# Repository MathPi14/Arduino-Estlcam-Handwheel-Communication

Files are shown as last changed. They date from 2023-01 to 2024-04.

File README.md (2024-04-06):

# [GERMAN VERSION](https://github.com/MathPi14/Arduino-Estlcam-Handwheel-Communication/blob/main/README_DE.md)

# Table of contents
* [General Description](#general-description)
* [Prerequisites](#prerequisites)
* [Installation](#installation)
* [Used Components](#used-components)

## General Description
This is my implementation of the Estlcam handwheel i2c communication protocol (https://www.estlcam.de/DIN_Detail.php) for Arduino Boards. 
Its made for users of the original Estlcam Hardware.

The Code supports all the features the originial handwheel provides:
* 3/4 - axis joystick for rough positioning 
* encoder (handwheel) which allows very fine positioning
* spindle, program start and enter (probing) buttons 
* feed and speed override potentiometers

the following 'hidden' features are implemented as well:
* 3 led which indicate which of the axis is currently active to move on the handwheel
* 3 buttons to change the currently active axis 
* emergency stop (triggers program pause)

top
inside
inside_2
Unbenannt

Tested with Estlcam V11.244. The hidden features may not be supported by other Estlcam Versions.
	
## Prerequisites
To get started, you need the following:
* an original Estlcam board with a mini-DIN port
* mini-DIN cable (6 Pin, male connector). 2-3 m length recommended, depending on the size of your cnc. Super long cables (>5 m) might cause EMC issues
* an arduino (original or compatible) board with 5 V operating voltage, 7 ADC Pins including SDA and SCL for the i2c communication functionality and 9 digital Pins like the Arduino Nano 
* analog joystick (3 or 4 axis, 10kohm)
* handwheel encoder
* 2x 10kohm potentiometers
* 6x push buttons. No toggle switches!
* 3x 5 V LED (or 12 V with appropiate resistor)
* emergency stop button
* housing (see attached .stl files)
* a small cable gland (M16/ PG9 if you use my 3d printed housing)
* 4 M4 brass inserts and short screws (if you use my 3d printed housing)

You also need basic soldering equipment, cables, shrink tubing, hot glue etc.
	
## Installation
### Housing/ Electronics
* start with installing the led, push-buttons, the encoder and potentiometers (not the joystick, arduino, cable gland and emergency stop for now). Carefully solder (not too short) cables to the components. It's recommended to use the screw terminals of the handwheel encoder as bus for the components and the DIN Cable as well. This way, the DIN cable remains detatchable
* secure the cables with hot glue
* solder the cables to the arduino according the attached photo of the pinout. Use two short cables for the SDA and SCL so that we can connect them to the DIN cable with Wago clamps later (the cable remains detachable, see #1)
* attach the arduino to the insert and sort the cables with the cable comb
* insert the DIN cable, connect enc + and - as well as VCC and GND to the encoder (handwheel) and SDA/ SCL to the arduino

### Software (Arduino)
Flash the Arduino via the IDE. The onboard TX LED blinks when the program is running. 
If you use any other arduino board or if your pin assignment differs from mine, you may need to change the following defines 

```
#define JOYSTICK_X_GPIO A0            
#define JOYSTICK_Y_GPIO A1
#define JOYSTICK_Z_GPIO A2
#define SPEED_GPIO A6                  
#define SPEED_GPIO_INVERTED 1          
#define FEED_GPIO A7                   
#define FEED_GPIO_INVERTED 1            

#define X_LED_GPIO 2
#define Y_LED_GPIO 3
#define Z_LED_GPIO 4

#define X_SELECT_GPIO 5
#define Y_SELECT_GPIO 6
#define Z_SELECT_GPIO 7          
#define SPINDLE_START_GPIO 8    
#define PROGRAM_START_GPIO 9
#define OK_GPIO 10                   
#define STOP_GPIO 11         

#define ONBOARD_LED_GPIO 13           
```

### Software (Estlcam)
After the electrical work is done and the Code is running on your Arduino, you can connect the mini-DIN cable to the Estlcam Board and reprogram the latter. You know that everything worked out, if there's a 'Handrad 0001 ...' line appearing in the log inside Estlcam. If it didn't, there is most likely something wrong with the SDA/ SCL Pins.

If it works, you can go to the controls tab inside Estlcam and test the components. If the Joystick ADC are inverted, you can simply change it in Estlcam directly. If the Buttons, LED or feed/ speed potentiometers are inverted or not assigned correctly, go back to the previous step and change the defines

## Used Components
* joystick (https://de.aliexpress.com/item/4001270851701.html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)
* encoder (5V 4Pin, 60 mm) (https://de.aliexpress.com/item/32949618549.html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)
* buttons (https://de.aliexpress.com/item/1005003302861259.html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)
* 5V led (https://de.aliexpress.com/item/1005003751324053.html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) 
* 10 kOhm potentiometers (https://de.aliexpress.com/item/4000971762879.html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)
* emergency stop (16 mm diameter) (https://de.aliexpress.com/item/33014058927.html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)
* Arduino Nano (https://de.aliexpress.com/item/1005002867053794.html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)

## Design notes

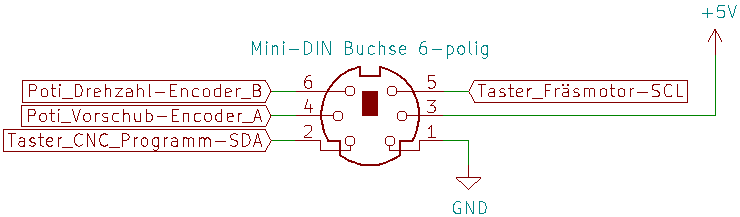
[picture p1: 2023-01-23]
DIN_cable.png

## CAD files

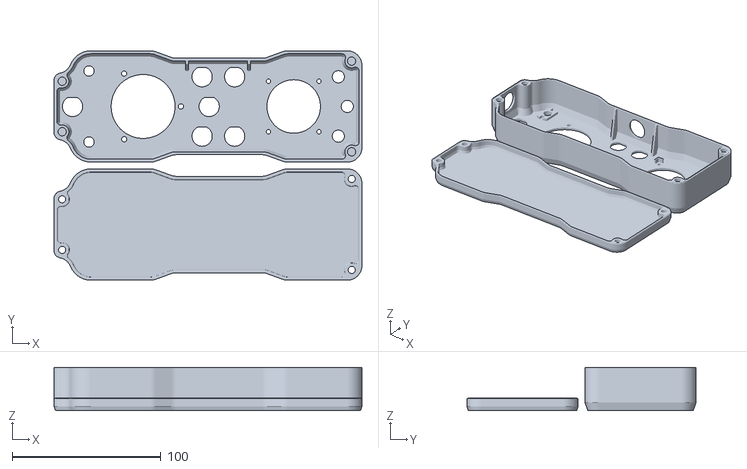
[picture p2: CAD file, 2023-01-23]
housing.stl
207.4 x 154.5 x 29.0

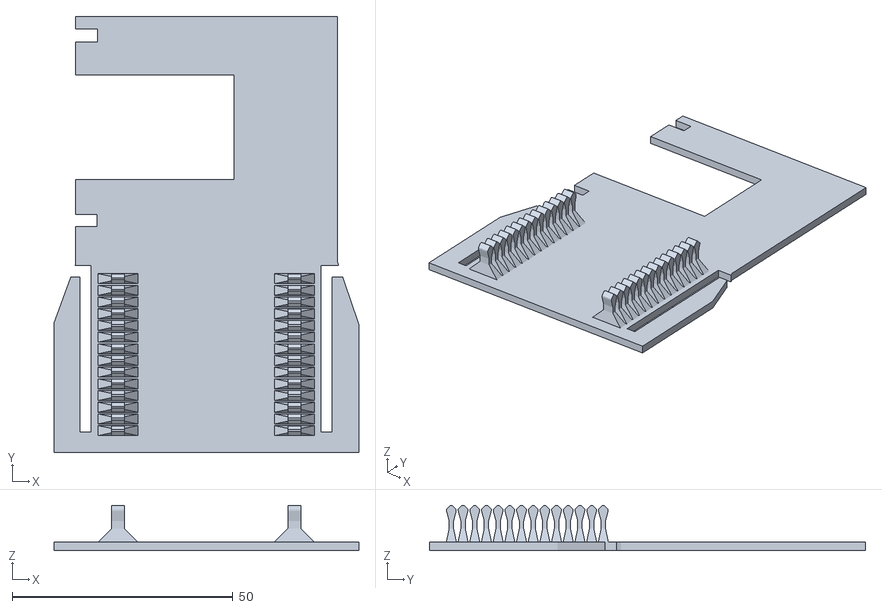
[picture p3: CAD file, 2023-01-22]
insert.stl
69.1 x 98.9 x 10.3

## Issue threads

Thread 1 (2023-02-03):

Use HWInterrupts instead of polling to register changing states of all buttons

MathPi14, 2023-02-03:
Not all Arduinos come with 5 Interrupt Pins. In oder to make the code less dependent from the used hardware, polling is used to register button change "events". This can lead to a sluggish response.

In a future release, PinChangeInterrupts (see Arduino site) shall be used to solve this problem. These dont work like "normal" Interrupts and always trigger on both the rising and falling edge. Debouncing and faster Read/ Write cycles (e.g. with direct port manipulation) are necessary.

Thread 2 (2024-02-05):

old vs new version - potentiometers do not work

KaHu85, 2024-02-05:
Hello MathPi14,

we are having a [discussion here](https://www.cnc-aus-holz.at/index.php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) about the old and new code.
Somehow the new code does not work with the pots.
Found the old code from 21.7.2022,
now the potentiometers work.

Can you have a look over it?
It's just the calculation for the potentiometers that's different, isn't it?

Would be great if you could take a look at it and shed some light on why it doesn't work with the new code.
Regards Alex

KaHu85, 2024-02-06:
Hallo Matthias, ah okay...
Ja ich habe es dann nur mal verglichen alt mit neu und die Zahlen die raus kommen sind aber annähernd gleich. Deshalb habe ich es nicht verstanden wieso es mit der alten Version scheinbar funktioniert. Jedenfalls konnte ich ihnen etwas helfen, Sie haben es jetzt zum laufen gebracht, jedoch witzigerweise nur bis zu einer gewissen Estlcam Version. Keine Ahnung was da in Estlcam geändert wurde wieso es dann aufeinmal nicht mehr geht. Danke und bis bald. LG Alex

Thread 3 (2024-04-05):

Schaltplan

Tino51078, 2024-04-05:
Hallo Matthias,

ich bin durch Zufall auf dein Projekt gestoßen und würde das gerne nachbauen. Leider fehlt mir ein wenig (viel) Erfahrung mit den Arduino´s. Ich habe mal versucht deinen Aufbau in einem Schaltplan zusammenzufassen. Leider kann ich nicht allen in deinem Gehäuse erkennen. Somit kann natürlich erstmal nicht alles in dem Plan stimmen. Es wäre sehr freundlich von dir, wenn du dir bei Gelegenheit die Zeit nehmen könntest um die Fehlenden Sachen zu korrigieren. Wenn du willst, kann ich dann den fertigen, geänderten Plan zu deiner Bauanleitung bereitstellen. Würde mich über deine Unterstützung sehr freuen.

Viele Grüße
Tino
[Schaltplan.pdf](https://github.com/MathPi14/Arduino-Estlcam-Handwheel-Communication/files/14890862/Schaltplan.pdf)

MathPi14, 2024-04-06:
Hallo Tino, ich habe meinen Schaltplan erweitert. Habe zwar leider kein so tolles CAD Programm wie du, aber das sollte dir weiterhelfen. Es kann natürlich vorkommen, dass die Farbcodierung der Chinesen mal abweicht (Joystick), also würde vorschlagen, dass du die Belegung vorher testest z. B. mit Multimeter. Alternative: Trial and Error am Arduino.
Gruß Matthias

Tino51078, 2024-04-06:
Hallo Matthias,
jetzt bin ich ein wenig verwirrt. an die 5 Potis müssen bestimmt je 3 Kabel. (+/-und die Funktion)Bedeutet bestimmt die roten Leitungen aus deinem Schaltplan liegen am Mittelanschluss und die jetzigen roten am Poti wären 5v. Vermute ich mal. Aber mehr verwirrt mich der encoder. In deinem Aufbau ist definitiv 0V und Vcc belegt nicht A&B. Tut mir leid, ich will dir nicht auf die Nerven gehen. Möchte nur keine Fehler einbauen und defekte provozieren.....  Nochmal kurz zu meiner Frage bei "CNC aus Holz"
Mit dem Arduino UNO wird dein Aufbau so nicht gehen, Oder? Weil der weniger PIN´s als der NANO hat...?

Grüße Tino

MathPi14, 2024-04-06:
> an die 5 Potis müssen bestimmt je 3 Kabel. (+/-und die Funktion)Bedeutet bestimmt die roten Leitungen aus deinem Schaltplan liegen am Mittelanschluss und die jetzigen roten am Poti wären 5v
Der Mittlere Anschluss an den Potis ist immer das Signal, die anderen beiden GND und VCC (kann man auch vertauschen, dann ist das Signal physisch invertiert - Achse fährt verkehrt herum -, kann aber logisch in Estlcam wieder "umgedreht" werden. Bei den Geschwindigkeits-Potis muss man im Code ein Flag setzen (da bietet Estlcam keine Möglichkeit)

> Aber mehr verwirrt mich der encoder. In deinem Aufbau ist definitiv 0V und Vcc belegt nicht A&B
GND und VCC müssen schon auch belegt werden, sonst funktioniert der Encoder nicht. Die beiden **nicht belegten** anschlüsse sind dann Encoder A und B. Der Anschluss der Mini-Din-Buchse (dort sind die Kabel für Enc A/B) ist nicht auf den Bildern drauf, da man sonst nichts mehr erkennen würde :)

> Mit dem Arduino UNO wird dein Aufbau so nicht gehen, Oder?
Richtig

Du nervst nicht, mein Plan ist natürlich eine Bastlerlösung und deswegen sehr grob. Daher ja auch der Hinweis, dass man idealerweise etwas Erfahrung und (bei solchen DIY Projekten sowieso) Frusttoleranz mitbringen sollte.

hope that helps
Matthias

Tino51078, 2024-04-06:
Matthias,

vielen vielen ank für die Unterstützung. Ja ich habe schon in einigen Sachen Erfahrung. Ich lerne aber auch gerne dazu. Dabei möchte ich gerne soviel Fehlerquellen wie möglich vorab ausschließen. Deshalb auch meine vielen Nachfragen. Ich würde sehr gerne den Plan mit allen Komponenten nochmal zeichnen. Vielleicht kannst du dann nochmal drüber schauen? Ich konnte ja deinen Neid über mein CAD durchs WLAN spüren... Nein, ist nur Spaß... Aber falls der Plan dann okay ist, kann er auch gerne in deine Doku, falls du das möchtest. Ich werde jetzt auch nach deinem Vorbild zeichnen, der ist deutlich übersichtlicher.

Tino51078, 2024-04-06:
> Du nervst nicht, mein Plan ist natürlich eine Bastlerlösung und deshalb sehr grob. Daher ja auch der Hinweis, dass man idealerweise etwas Erfahrung und (bei solchen DIY-Projekten sowieso) Frusttoleranz mitbringen sollte.

Eine Bastlerlösung ist das bei weitem nichtmehr. Das ist schon ein nahezu perfektes Projekt. Die Gedanken dazu soll sich erstmal einer machen...

Tino51078, 2024-04-06:
Ich denke, so sollte es passen. Sind jetzt alle Komponenten drauf...
[Schaltplan Handrad.pdf](https://github.com/MathPi14/Arduino-Estlcam-Handwheel-Communication/files/14893951/Schaltplan.Handrad.pdf)

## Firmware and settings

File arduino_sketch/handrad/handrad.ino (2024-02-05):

/*
  Created on 21.07.2022 by MathPi 
  https://github.com/MathPi14/Arduino-Estlcam-Handwheel-Communication/edit/main/README.md#used-components      
*/

#include <Wire.h>

#define JOYSTICK_X_GPIO A0              // ADC Pins the Joystick, speed, feed ovveride potis are connected to
#define JOYSTICK_Y_GPIO A1
#define JOYSTICK_Z_GPIO A2
#define SPEED_GPIO A6                  
#define SPEED_GPIO_INVERTED 1          // 1 if the Poti values shall be inverted 
#define FEED_GPIO A7                   
#define FEED_GPIO_INVERTED 1            // see above

#define X_LED_GPIO 2
#define Y_LED_GPIO 3
#define Z_LED_GPIO 4

#define X_SELECT_GPIO 5                 // Digital IO the corresp. buttons are connected to
#define Y_SELECT_GPIO 6
#define Z_SELECT_GPIO 7
#define PROGRAM_START_GPIO 8           
#define SPINDLE_START_GPIO 9           
#define OK_GPIO 10                   
#define STOP_GPIO 11

#define ONBOARD_LED_GPIO 13             // "-" onboard led

#define DEBUG 0

#define I2C_ADRESS 0b0000010            // I2C Slave Adress
#define I2C_CLOCK_FREQUENCY 10000       // I2C Clock Frequency
#define IDENT_STRING "Handrad 0001"     // Response to Mode3: Identify
#define SERIALNO_STRING "ABCD12345678"  // Response to Mode5: Serial Number
#define READ_FRAME_SIZE 9               // Number of incoming Bytes on I2C Receive event
#define SEND_FRAME_SIZE 15              // "-" outgoing Bytes on I2C Request event

const uint8_t CHALLENGE_VAL[] = {0x3B, 0x59, 0xE8, 0x2A, 0xE9, 0xB1, 0xBE, 0xD8, 0x00, 0x00, 0x00, 0x00}; //Response to Mode5: Challenge
volatile uint8_t rcv_frame[9];          // 9 byte buffer for the received frames, needs to be volatile because it is changed on hardware interrupts
uint8_t send_frame[15];                 // 15 byte array for the values to send, must not be volatile because they are only updated in the loop()
volatile uint16_t speed_data;                    // 2 byte value for the analog speed ovveride (on SPEED_GPIO)
volatile uint16_t feed_data;                     // same as above
volatile uint16_t x_data;
volatile int16_t y_data;
volatile uint16_t z_data;
volatile uint8_t crc;                            // 1 byte value for the checksum (byte 15)
volatile bool program_start_btn_pressed;
volatile bool spindle_start_btn_pressed;
volatile bool ok_btn_pressed;
volatile bool stop_btn_pressed;
volatile uint8_t axis_selected;

// setup called once on program start
void setup() {
  Wire.begin(I2C_ADRESS);               // initialize device as peripheral with I2C_ADRESS (specified by Estlcam)
  Wire.setClock(I2C_CLOCK_FREQUENCY);   // set clock frequency to I2C_CLOCK_FREQUENCY (specified by Estlcam)
  Wire.onRequest(RequestEventHandler);  // register RequestEventHandler on Request Events from the Master (Estlcam)
  Wire.onReceive(ReceiveEventHandler);  // register ReceiveEventHandler on Receive Events from the Master (Estlcam)
  pinMode(PROGRAM_START_GPIO, INPUT_PULLUP);                    // initialize Button and Led GPIOs
  pinMode(SPINDLE_START_GPIO, INPUT_PULLUP);
  pinMode(OK_GPIO, INPUT_PULLUP);
  pinMode(STOP_GPIO, INPUT_PULLUP);
  pinMode(X_SELECT_GPIO, INPUT_PULLUP);
  pinMode(Y_SELECT_GPIO, INPUT_PULLUP);
  pinMode(Z_SELECT_GPIO, INPUT_PULLUP);
  pinMode(X_LED_GPIO, OUTPUT);
  pinMode(Y_LED_GPIO, OUTPUT);
  pinMode(Z_LED_GPIO, OUTPUT);
  pinMode(ONBOARD_LED_GPIO, OUTPUT);
#ifdef DEBUG
  Serial.begin(9600);
  Serial.println("Running");
#endif
}

// loop is called constantly
// handle mode state machine specified by Estlcam
void loop() {
  buffer_data();
  switch (rcv_frame[0]) 
  {
    case 0:
      delay(100);
      break;

    case 1:
      update_data();                                // update mode specific data
      break;

    case 2:
      update_data();                                // update mode specific data
      update_status_led();
      break;

    case 3:
      identify();
      break;

    case 4:
      challenge();
      break;

    case 5:
      serialnumber();
      break;
  }
}

//
void update_status_led() {
  switch (rcv_frame[1]) {
    case 0:
      digitalWrite(X_LED_GPIO, 0);
      digitalWrite(Y_LED_GPIO, 0);
      digitalWrite(Z_LED_GPIO, 0);
      break;

    case 1:
      digitalWrite(X_LED_GPIO, 1);
      digitalWrite(Y_LED_GPIO, 0);
      digitalWrite(Z_LED_GPIO, 0);
      break;

    case 2:
      digitalWrite(X_LED_GPIO, 0);
      digitalWrite(Y_LED_GPIO, 1);
      digitalWrite(Z_LED_GPIO, 0);
      break;

    case 4:
      digitalWrite(X_LED_GPIO, 0);
      digitalWrite(Y_LED_GPIO, 0);
      digitalWrite(Z_LED_GPIO, 1);
      break;
  }
}
// called on a i2c Request from the Master (Estlcam)
// interrupts the loop() thus needs to be as fast as possible
// increment Frame number and checksum according to Specification from Estlcam
void RequestEventHandler() {
  if (rcv_frame[0] != 0) {
    send_frame[12] = rcv_frame[0];                // set 12 bit to match selected mode
    send_frame[13] += 1;                          // increment frame on 13 byte
    send_frame[14] = crc_calc();                  // calculate checksum on 14 byte
    Wire.write(send_frame, sizeof(send_frame));   // Write new frame to the Master
  }
#ifdef DEBUG
  Serial.print("received : ");
  for (int i = 0; i < READ_FRAME_SIZE; i++) {
    if ((int)rcv_frame[i] < 20) {
      Serial.print("0");
    }
    Serial.print(rcv_frame[i], HEX);
    Serial.print(" ");
  }
  Serial.print("; sending: ");
  for (int i = 0; i < SEND_FRAME_SIZE; i++) {
    if ((int)send_frame[i] < 20) {
      Serial.print("0");
    }
    Serial.print(send_frame[i], HEX);
    Serial.print(" ");
  }
  Serial.println("");
#endif
}

// called on a i2c Request from the Master (Estlcam)
// interrupts the loop() thus needs to be as fast as possible and needs a volatile buffer to write data to
// save byte 1 of the received frame (specifies the  mode used in the loop() state machine)
void ReceiveEventHandler(int rcv_frame_size) {
  if (rcv_frame_size == READ_FRAME_SIZE) {        // check if we receive 9 bytes (according to specification from Estlcam)
    for (int i = 0; i < READ_FRAME_SIZE; i++) {   // save received data byte-by-byte to the volatile buffer variable
      rcv_frame[i] = Wire.read();
    }
  }
#ifdef DEBUG
  Serial.println("Receive Request");
#endif
}

void update_data() {
  send_frame[0] = 0xFF;                     //byte 1 = 255 according to spec
  if (axis_selected > 0) {
    send_frame[0] &= ~(1 << axis_selected - 1) | (0 << axis_selected - 1);
  }

  send_frame[1] = 0xFF;                     //set bits 2, 4,5,6,7 of byte 2 to 1 beforehand
  if (!program_start_btn_pressed) {
    send_frame[1] &= ~(1 << 0) | (0 << 0); //flip bit 0 if PROGRAM_START_GPIO is high
  }
  if (!spindle_start_btn_pressed) {
    send_frame[1] &= ~(1 << 1) | (0 << 1); //flip bit 1 if SPINDLE_START_GPIO is high
  }
  if (!ok_btn_pressed) {
    send_frame[1] &= ~(1 << 3) | (0 << 3); //flip bit 3 if OK_GPIO is high
  }
  if (stop_btn_pressed) {
    send_frame[1] &= ~(1 << 2) | (0 << 2); // stop
  }

  send_frame[2] = lowByte(speed_data);
  send_frame[3] = highByte(speed_data);
  send_frame[4] = lowByte(feed_data);
  send_frame[5] = highByte(feed_data);
  send_frame[6] = lowByte(x_data);
  send_frame[7] = highByte(x_data);
  send_frame[8] = lowByte(y_data);
  send_frame[9] = highByte(y_data);
  send_frame[10] = lowByte(z_data);
  send_frame[11] = highByte(z_data);
}

// called once after a Request Event fired and we are in mode 1
// update the data to write out to the master
void buffer_data() {
  program_start_btn_pressed = digitalRead(PROGRAM_START_GPIO);
  spindle_start_btn_pressed = digitalRead(SPINDLE_START_GPIO);
  ok_btn_pressed = digitalRead(OK_GPIO);
  stop_btn_pressed = digitalRead(STOP_GPIO);
  if (digitalRead(X_SELECT_GPIO) == 0) {
    axis_selected = 1;
  }
  else if (digitalRead(Y_SELECT_GPIO) == 0) {
    axis_selected = 2;
  }
  else if (digitalRead(Z_SELECT_GPIO) == 0) {
    axis_selected = 3;
  }
  else {
    axis_selected = 0;
  }
  speed_data = SPEED_GPIO_INVERTED ? 65535 - (analogRead(SPEED_GPIO) * 64) : analogRead(SPEED_GPIO) * 64;
  feed_data = FEED_GPIO_INVERTED ? 65535 - (analogRead(FEED_GPIO) * 64) : analogRead(FEED_GPIO) * 64;
  x_data = analogRead(JOYSTICK_X_GPIO) * 64;// convert the returning 10 bit uint from analogRead() to a 16 bit uint 
  y_data = analogRead(JOYSTICK_Y_GPIO) * 64;
  z_data = analogRead(JOYSTICK_Z_GPIO) * 64;
}

// called once after a Request Event fired and we are in mode 3
// update the data to write out to the master
void identify() {
  for (int i = 0; i < 12; i++) {
    send_frame[i] = IDENT_STRING[i];
  }
};

// called once after a Request Event fired and we are in mode 4
// update the data to write out to the master
void challenge() {
  for (int i = 0; i < 12; i++) {
    send_frame[i] = CHALLENGE_VAL[i];
  }
}

// called once after a Request Event fired and we are in mode 5
// update the data to write out to the master
void serialnumber() {
  for (int i = 0; i < 12; i++) {
    send_frame[i] = SERIALNO_STRING[i];
  }
}

// calculate the checksum according to specification from Estlcam
uint8_t crc_calc() {
  crc = 0;                                  //clear checksum
  for (int i = 0; i < 14; i++) {            //for bytes 1-14: XOR next byte with current checksum, then increment the latter
    crc ^= send_frame[i];
    crc++;
  }
  return crc;
}

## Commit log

2023-01-11 arduino code uploaded
2023-01-22 Update README.md
    added description for emergency button and pictures
2023-01-22 Update handrad.ino
    cleanup, changed pin assignment
2023-01-22 Uploaded housing 3D files
    [housing.stl, insert.stl]
2023-01-23 updated housing (better fit when printed with a 0.4 mm nozzle)
    [housing.stl]
2023-01-23 added picture of the DIN cable wire specification
2023-01-24 added an eyelet to the housing model
    [insert.stl]
2023-01-24 optimized housing model, making it easier to print
2023-02-03 reverted some changes in handrad.ino, that caused the hardware interrupts to not work properly
    [handrad.ino]
2023-03-20 - moved handrad.ino inside a sketch folder - fixed a bug that affected the potentiometer data scaling
    [handrad.ino]
2024-02-05 reverted Changes to the calculation of the joystick data
    [handrad.ino]
